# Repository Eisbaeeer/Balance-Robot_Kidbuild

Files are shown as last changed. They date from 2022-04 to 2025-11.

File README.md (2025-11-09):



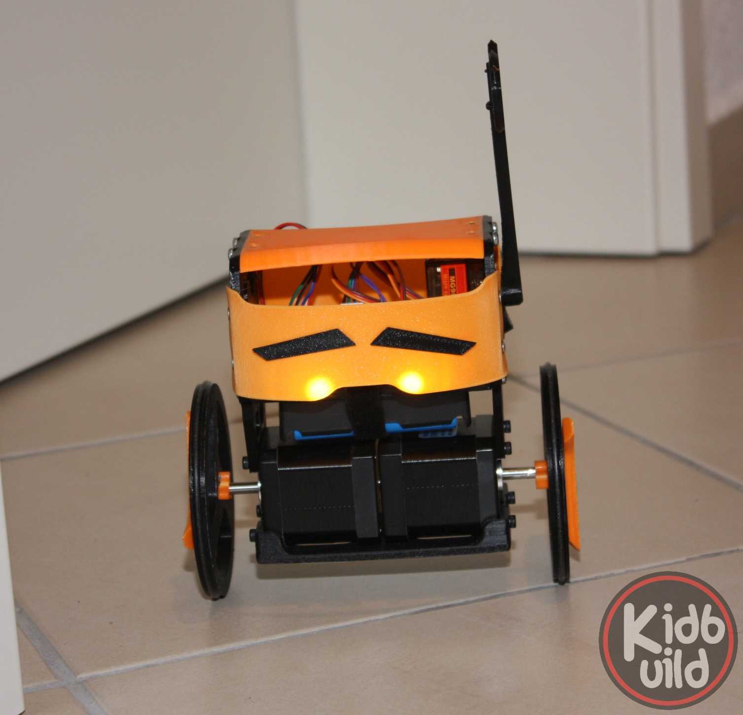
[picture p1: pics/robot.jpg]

# Balance-robot Kidbuild 

## Description
Build your own balanced robot with this project. Based on jjrobots and bluino.com we present an 
open source balanced robot with enhanced features.

## Features
- The source is merged to the platformio enviroment.
- The project is open source. You can build up your own robot for free (only hardware costs).
- The project use standard hardware like stepper, driver, electronics. You can buy it as you like.
- Use the project for education!
- Control the robot via android app

## STL files for 3D printing
You will find all STL files and addons in the STL folder. Typically printed without support.
0.2mm thickness and 20% infill should work well.

## Electronic schematic

| Pin | Function |
|---|---|
| 12 | Stepper A&B Enable | 
| 26 | Stepper A STEP |
| 25 | Stepper A DIR |
| 14 | Stepper B STEP |
| 27 | Stepper B DIR |
| 13 | Servo |
| 21 | MPU-6050 SDA |
| 22 | MPU-6050 SCL |
| 32 | LED Light |
| 33 | BUZZER |

## HMTL commands

| Command Character 	|HTML command after IP/URL  |
|---|---|
| Forward | /?fader1=1.00 |
| Backward | /?fader1=0.00 |
| Turn Right | /?fader2=0.00 |
| Turn Left | /?fader2=1.00 |
| Servo Arm | /?push1=1|2 |
| Beep On|Off 	 | /?push3=1|2 |
| Turn Light On|Off | /?push4=1|0 |
| Mode PRO On|Off | /?toggle1=1|0 |
| P-Stability | /?fader3=0.00-1.00 |
| D-Stability | /?fader4=0.00-1.00 |
| P-Speed | /?fader5=0.00-1.00 |
| I-Speed | /?fader6=0.00-1.00 |

## BOM

| Pieces | Description									|
|---|---|
| 1		 | PCB ESP32 Balancing Robot Shield				|
| 1		 | ESP32 DEVKIT V1 board 						|
| 2		 | Stepper Motor Driver A4988 					|
| 1		 | 3 axis Acc. and Gyro sensor MPU6050 			|
| 2		 | Stepper Motor Nema17 						|
| 1		 | Servo Motor MG90S/SG90						|
| 1		 | LED 3mm red									|
| 2		 | LED 3mm/5mm White Super Bright 				|
| 1		 | Active Buzzer 								|
| 2 	 | V-Regulator 5V AMS1117 SOT-223 (Kit is presoldered)	| 
| 1		 | Resistor 470 Ohm 								|
| 1		 | Capacitor 0.1uF 								|
| 1		 | Capacitor 100uF/16V rad.						| 	
| 2		 | Capacitor 220uF/16V rad.						|
| 1		 | Rocker Switch Dia. 20mm						| 
| 2		 | Rechargeable Battery Pack 2S Li-ion (2x 18650) 		| 
| 1		 | Micro USB Cable (optional for programming)	|
| 1		 | Terminal Screw 2 pin 5mm 					|
| 2		 | Female Header 15 pin 						|
| 5		 | Female Header 8 pin 							|
| 2		 | Female Header 4 pin 							|
| 1		 | Male Header 2 pin 							|
| 1		 | Male Header 3 pin 							|
| 2		 | Male Header 4 pin 							|
| 1		 | Jumper cap 									|
| 2		 | O-ring 3mm ID 82mm							| 
| 8		 | M3x8 screw									| 
| 9		 | M3x10 screw									|
| 9 | M3 nut |
| 12	 | self tapping screws 3mmx3mm					|

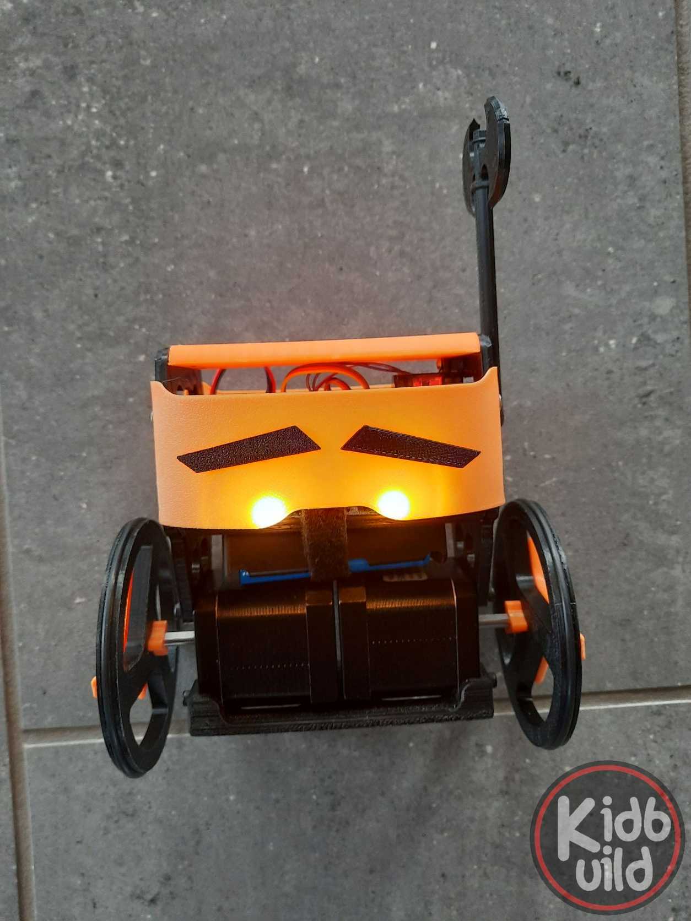
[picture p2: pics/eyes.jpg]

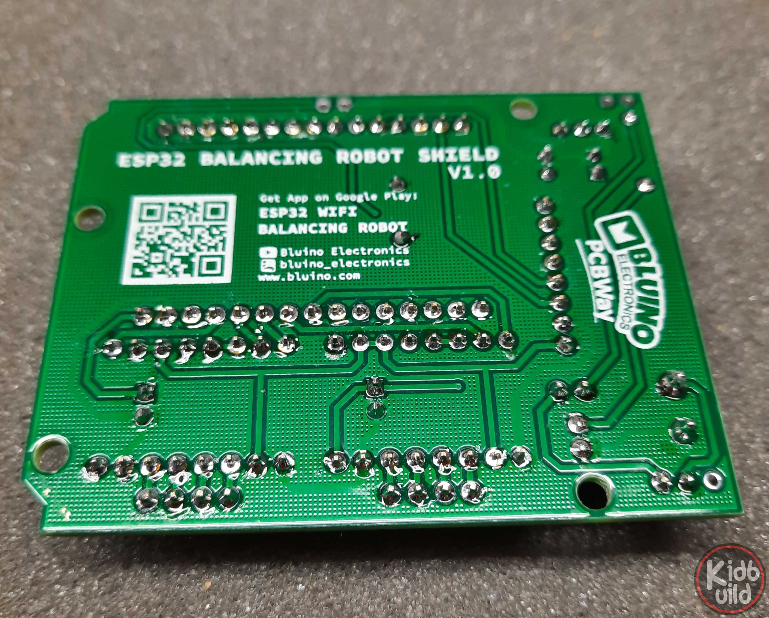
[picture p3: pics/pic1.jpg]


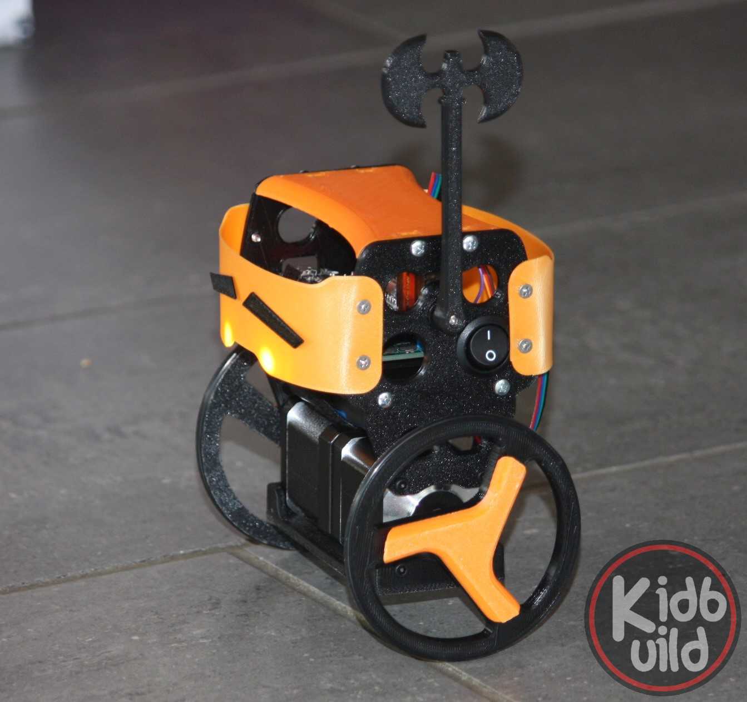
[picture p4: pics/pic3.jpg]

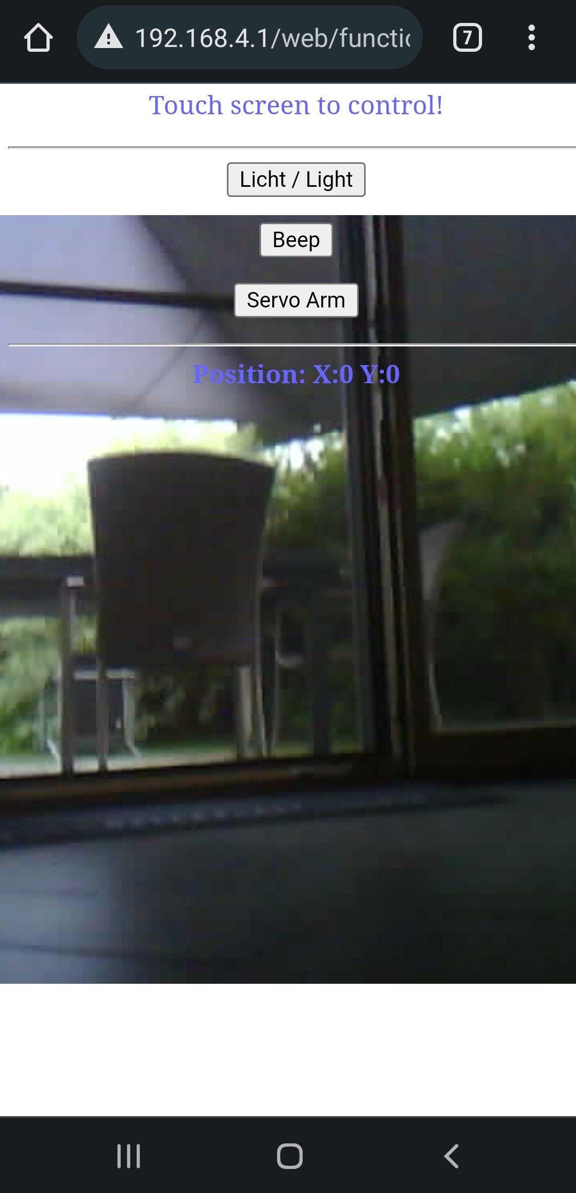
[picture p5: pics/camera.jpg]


## Wii Remote control
- Connect the Wii-Remote by pressing button 1 + 2 in same time
- Wii is connected, if LED one on Wii lit
- Hold the controller horizontal
- Button 1 = piezo
- Button 2 = eyes
- Button A = servo
- Controll via gyro by pressing the B button

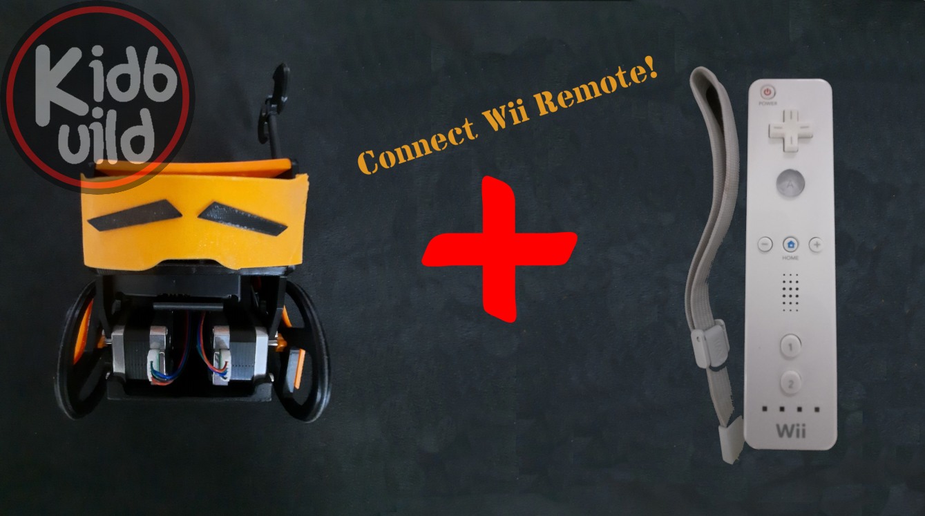
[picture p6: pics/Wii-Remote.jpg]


## How to flash

The easiest way to flash your Robot is to use the web flash tool.
Supported browser: Microsoft Edge or Google Chrome.
Follow this link for easy flashing: https://eisbaeeer.github.io/Balance-Robot_Kidbuild/flash/index.html

### Manual flashing
1. Donwload ESP flasher tool. E.g.: https://github.com/Jason2866/ESP_Flasher/releases
2. Download firmware.bin from release page: https://github.com/Eisbaeeer/Balance-Robot_Kidbuild/releases

## How to update via webUpdate
1. Connect to robot via Wifi
2. Open http://192.168.4.1/update
3. Upload firmware.bin from release page: https://github.com/Eisbaeeer/Balance-Robot_Kidbuild/releases 

## How to compile
1. Install VS-Code
2. Install addon platformio
3. clone repository
4. open repository in VS-Code
4. Compile

## Weblinks to get running
- http://www.kidbuild.de or https://shop.kidbuild.de
E-Mail info@kidbuild.de

## Changelog 

### Version 1.5
    Date: 20220819
    - Added passive buzzer support
    - Robot waiting 45 seconds for Wifi connection. After that the robot will disable Wifi and switch to Wii-remote bluetooth

### Version 1.4
    Date: 20220727
    - Added Wii-Remote as remote controller

### Verison 1.3
    Date: 20220703
    - Added OTA firmware web update
    - Optimized web control

### Version 1.2
	Date: 20220627
	- Added joystick via browser
	- Added background live view with esp32-camera
	- Added light, sound, servo control

### Version 1.0
    Date: 20220529
    Contributor: Kidbuild
    - Added Web control for any browser
    1. Connect to wifi of B-Robot
    2. Open browser at 192.168.4.1
    3. Take control via touch screen

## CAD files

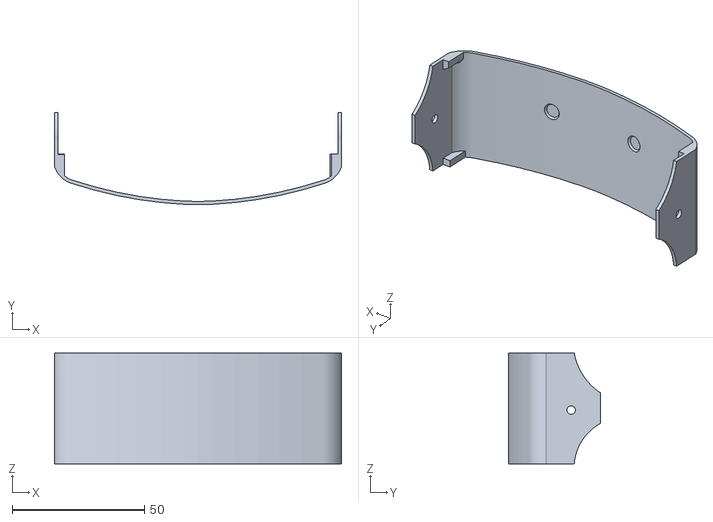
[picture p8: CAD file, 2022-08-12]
STL/2xFixed-Bumper_eyes.stl
108.5 x 34.9 x 41.9

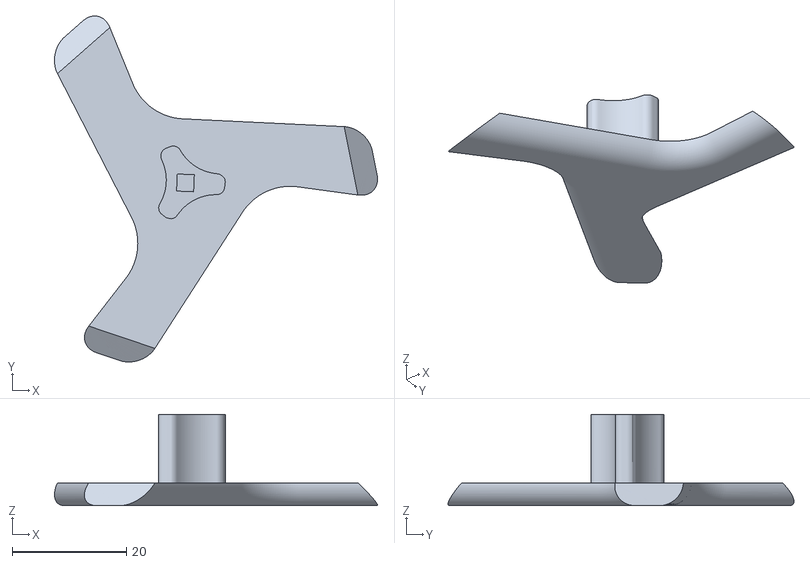
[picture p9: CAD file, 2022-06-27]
STL/Alternate_Hub-Wheel_4edges.stl
56.7 x 60.7 x 16.0

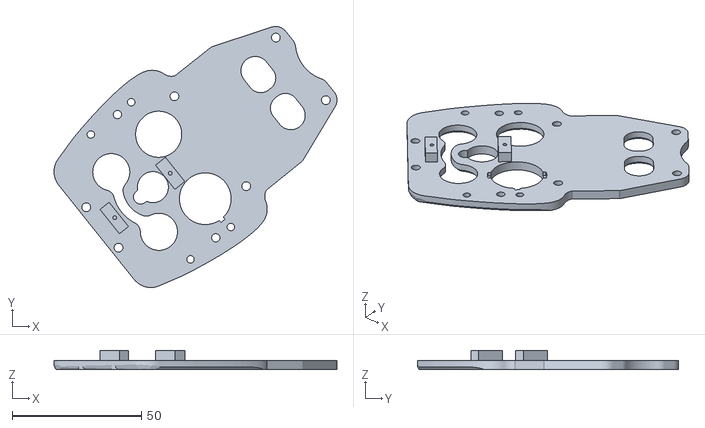
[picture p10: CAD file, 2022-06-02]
STL/1xSide_Panel_left_v3.stl
109.5 x 101.0 x 7.50

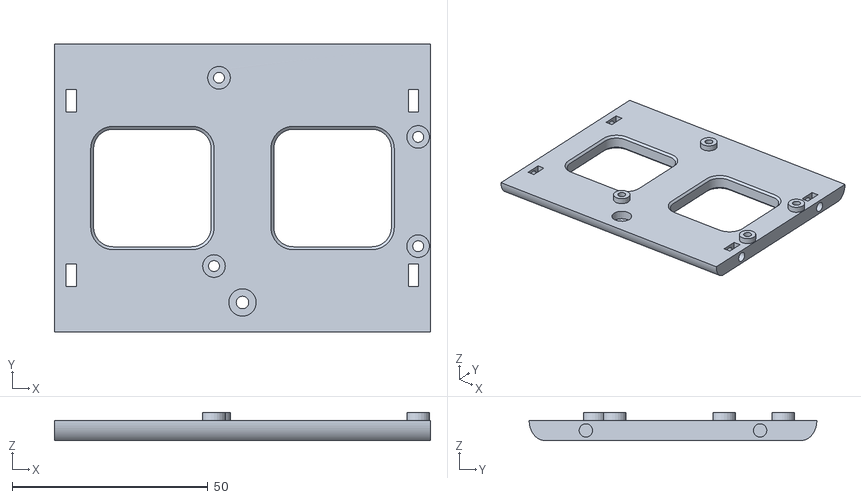
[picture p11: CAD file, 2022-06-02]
STL/1xElectronic_Shelf.stl
96.0 x 73.5 x 7.16

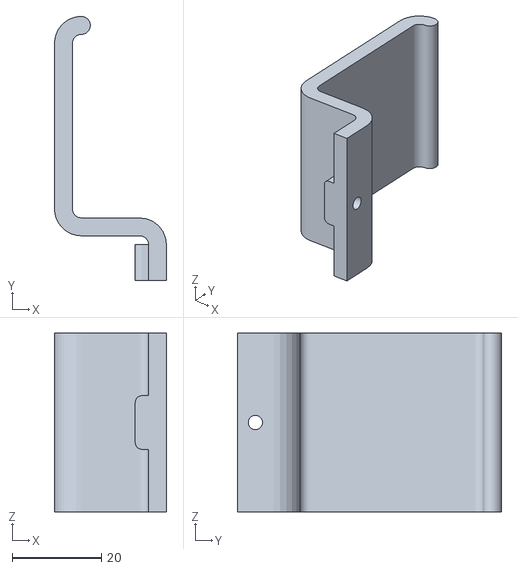
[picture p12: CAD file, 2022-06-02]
STL/1xBattery_holder_clip_2x18650.stl
25.0 x 59.0 x 40.0

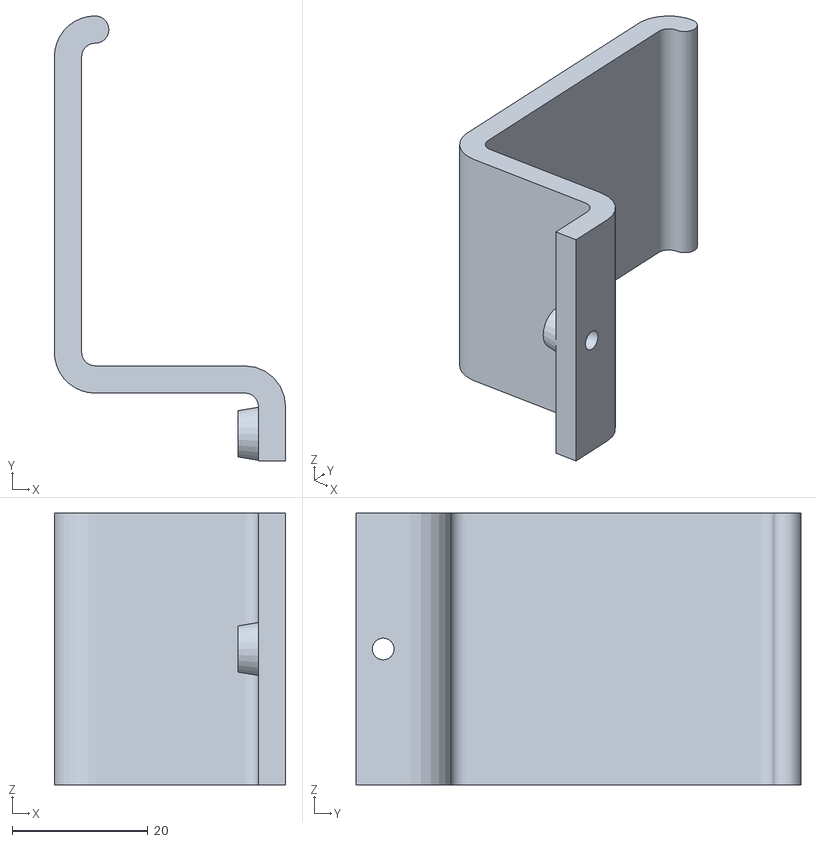
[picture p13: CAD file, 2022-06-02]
STL/1xBattery_holder_clip_6xAA.stl
34.0 x 65.4 x 40.0

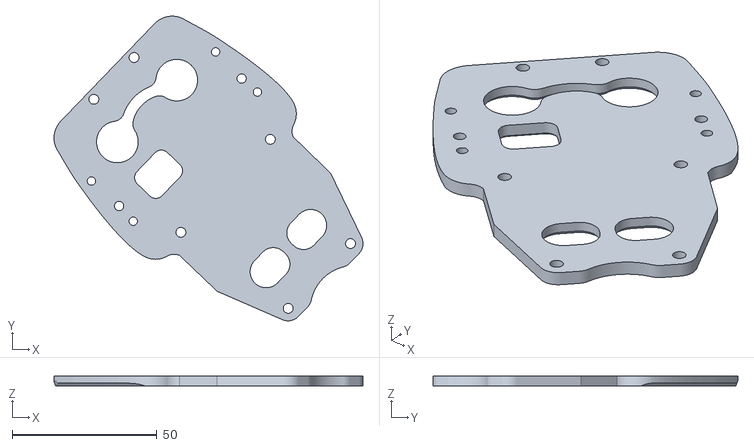
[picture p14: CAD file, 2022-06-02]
STL/1xSide_Panel_right_v3.stl
106.6 x 105.1 x 3.50

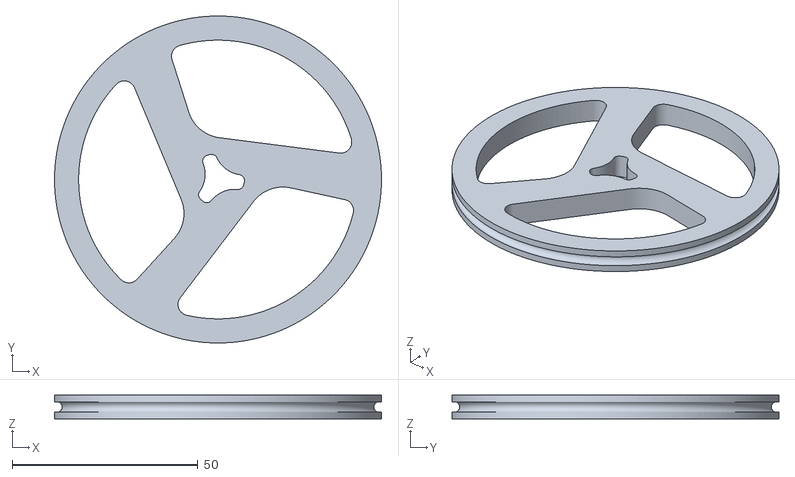
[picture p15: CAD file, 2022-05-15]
STL/2xWheel_FOR_O-RING.stl
88.0 x 88.0 x 6.40

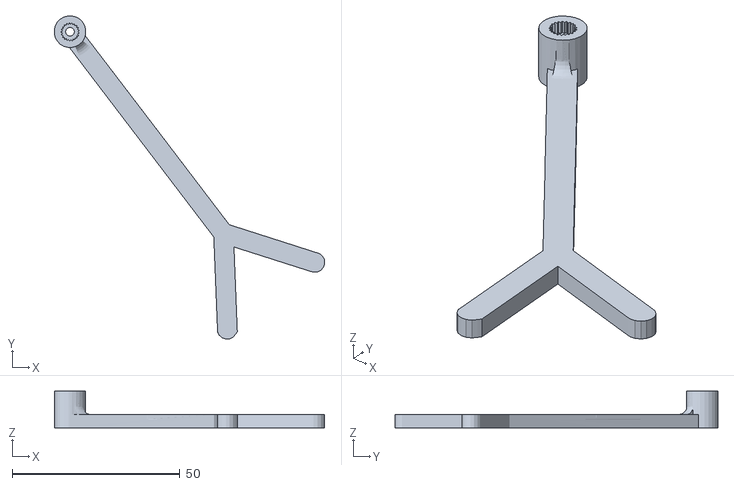
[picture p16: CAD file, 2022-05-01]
STL/1xregular-Arm-5mm.stl
80.6 x 96.3 x 11.0

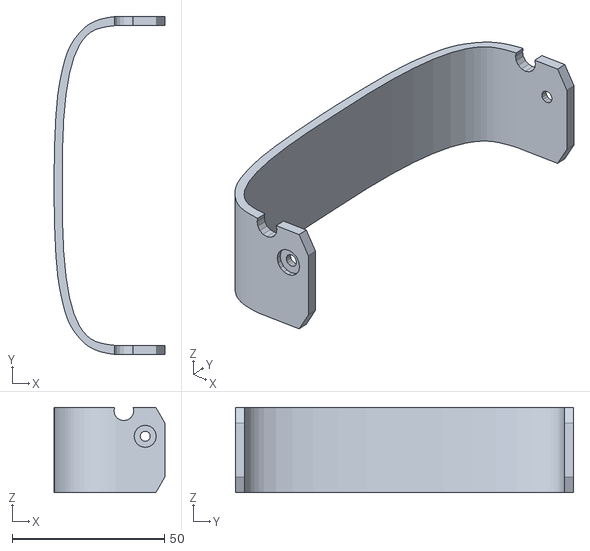
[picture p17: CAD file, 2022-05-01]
STL/ADDON_extra_bumper.stl
36.4 x 111.0 x 28.0

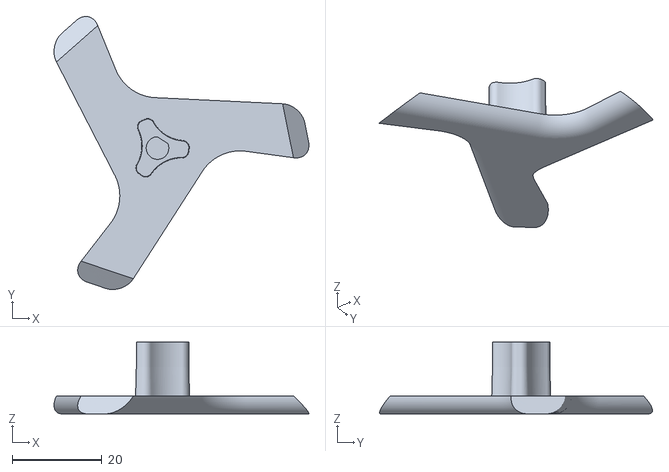
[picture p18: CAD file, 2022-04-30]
STL/2xHub_Wheel_ENLARGED.stl
56.7 x 60.7 x 15.9

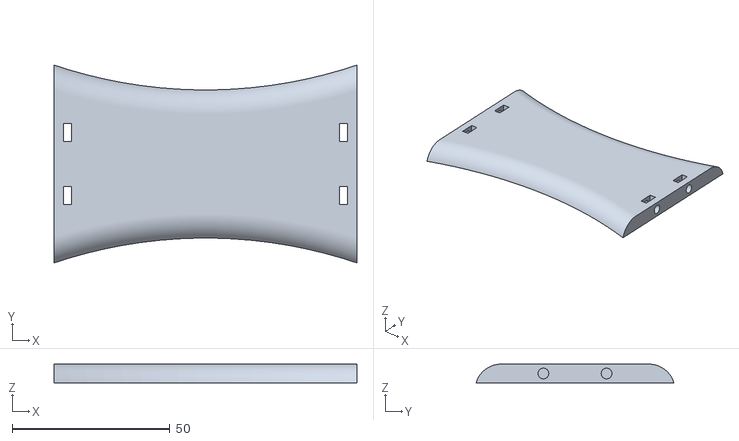
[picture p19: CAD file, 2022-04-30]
STL/1xTop_Shelf.stl
96.0 x 62.7 x 6.00

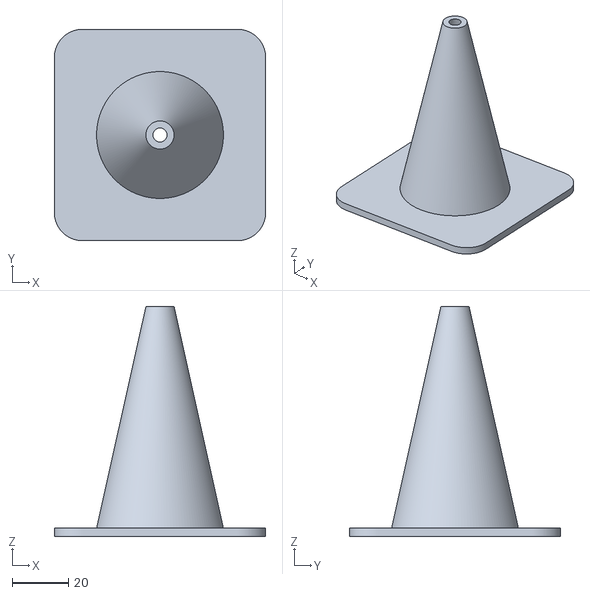
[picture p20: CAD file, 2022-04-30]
STL/ADDON._Traffic_Cone.stl
75.0 x 75.0 x 81.6

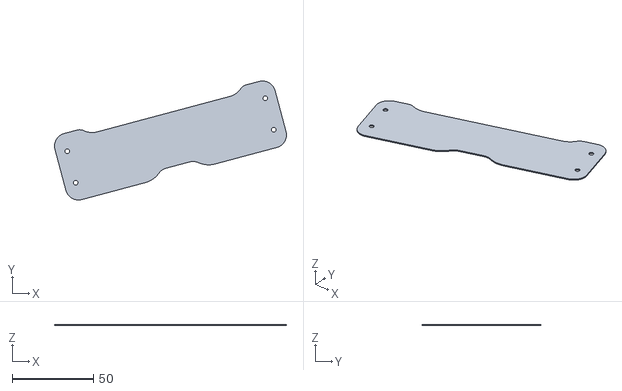
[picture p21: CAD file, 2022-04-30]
STL/2xBUMPER.stl
142.5 x 73.1 x 0.654

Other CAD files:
STL/ADDON_battle_axe_by_jfpion.stl
STL/ADDON_SKULL.stl
STL/ADDON.2xEyebrows.stl
STL/ADDON.1xTop_Shelf_for_CAN.stl
STL/1xMotor_Shelf.stl
STL/1xregular_ARM_6mm.stl
STL/ADDON.Top_Shelf_for_GoPro.stl
STL/ADDON_HOOK_ARM.stl
STL/ADDON_MACE_ARM.stl

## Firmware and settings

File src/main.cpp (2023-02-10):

/*
 *  Created on: 23.02.2021
 *      Author: anonymous
 * 
 *  Changelog:
 * 
 *  ### Version 1.5
 * (20221018)
 * - Added passive buzzer support
 * - Robot waiting 45 seconds for Wifi connection. After that the robot will disable Wifi and switch to Wii-remote bluetooth
 * 
    ### Version 1.4
 *  (20220727)
 *  - Added Wii-Remote as remote controller (pressing key 1 + 2 on same time to connect the Wii Remote)
 * 
 *  ### Verison 1.3
 *  (20220703)
 *  - Added OTA firmware web update
 *  - Optimized web control
 *
 *  ### Version 1.2
 *	(20220627)
 *	- Added joystick via browser
 *	- Added background live view with esp32-came
 *	- Added light, sound, servo control
 *
 *    ### Version 1.0
 *      (20220322)
 *      - Ported to platformio
 *      - Bugfix Android app right/left direction
 * 
 *  ToDo:
 *    - Web-GUI
 *    - OTA
 * 
 * ******** Pin out **********
 * Pin 12   Stepper A&B Enable
 * Pin 26   Stepper A STEP
 * Pin 25   Stepper A DIR
 * Pin 14   Stepper B STEP
 * Pin 27   Stepper B DIR
 * 
 * Pin 13   Servo
 * 
 * Pin 21   MPU-6050 SDA
 * Pin 22   MPU-6050 SCL
 * 
 * Pin 32   LED Light
 * 
 * Pin 33   BUZZER
 * 
 * ******** Command Character *******
 * Forward              /?fader1=1.00
 * Backward             /?fader1=0.00
 * Turn Right           /?fader2=0.00
 * Turn Left            /?fader2=1.00
 * Servo Arm            /?push1=1|2
 * Beep On|Off          /?push3=1|2
 * Turn Light On|Off    /?push4=1|0
 * Mode PRO On|Off      /?toggle1=1|0
 * P-Stability          /?fader3=0.00-1.00
 * D-Stability          /?fader4=0.00-1.00
 * P-Speed              /?fader5=0.00-1.00
 * I-Speed              /?fader6=0.00-1.00
 * 
 * Controll via Wii-Remote controller
 * - Connect to robot = press 1+2 same time
 * - Button 1         = piezo
 * - Button 2         = light
 * - Home             = toggle mode pro (pro mode lights blinking)
 * - Control via gyro = press B button + gyro move to go forward/backward right/left.
 *                      hold controller crosswise
 * 
 */
 
#include <Wire.h>
#include <WiFi.h>
#include <Arduino.h>
#include <AsyncTCP.h>
#include <ESPAsyncWebServer.h>
#include <AsyncElegantOTA.h>
#include "Control.h"
#include "MPU6050.h"
#include "Motors.h"
#include "defines.h"
#include "globals.h"
#include <stdio.h>
#include "esp_types.h"
#include "soc/timer_group_struct.h"
#include "driver/periph_ctrl.h"
#include "driver/timer.h"
#include "driver/ledc.h"
#include "esp32-hal-ledc.h"
#include "ESP32Wiimote.h"


const char* PARAM_FADER1 = "fader1";
const char* PARAM_FADER2 = "fader2";
const char* PARAM_PUSH1 = "push1";
const char* PARAM_PUSH2 = "push2";
const char* PARAM_PUSH3 = "push3";
const char* PARAM_PUSH4 = "push4";
const char* PARAM_TOGGLE1 = "toggle1";
const char* PARAM_FADER3 = "fader3";
const char* PARAM_FADER4 = "fader4";
const char* PARAM_FADER5 = "fader5";
const char* PARAM_FADER6 = "fader6";
//const char joystick_html[] PROGMEM="<html>\n\t <head>\n\t\t <meta charset=\"utf-8\">\n\t\t <meta name=\"viewport\" content=\"width=device-width, user-scalable=no, minimum-scale=1.0, maximum-scale=1.0\">\t\t\n\t\t <style>\n\t\t body {\n\t\t\toverflow\t: hidden;\n\t\t\tpadding\t\t: 0;\n\t\t\tmargin\t\t: 0;\n\t\t\tbackground-image\t: url('http://192.168.4.111:81/stream');\n\t\t\tbackground-repeat\t\t: no-repeat;\n\t\t\t}\n\t\t#info\n\t\t\t{\n\t\t\tcolor\t\t: #66F;\n\t\t\ttext-decoration\t: none;\n\t\t\tposition\t: absolute;\n\t\t\ttop\t\t: 0px;\n\t\t\twidth\t\t: 100%;\n\t\t\tpadding\t\t: 5px;\n\t\t\ttext-align\t: center;\n\t\t}\n\t\t#container {\n\t\t\twidth\t\t: 100%;\n\t\t\theight\t\t: 100%;\n\t\t\toverflow\t: hidden;\n\t\t\tpadding\t\t: 0;\n\t\t\tmargin\t\t: 0;\n\t\t\t-webkit-user-select\t: none;\n\t\t\t-moz-user-select\t: none;\n\t\t}\n\t\t</style>\n\n\t</head>\n\t<body>\n\n\t<div id=\"container\"></div>\n\n\t\n\n\t<div id=\"info\">Touch screen to control!\n\t\t\t<br>\n\t\t\t<p><b><hr><button onclick=\"window.location.href = '/web/function1.html'\">Licht / Light</button>\n\t\t\t<p><b><button onclick=\"window.location.href = '/web/function2.html'\">Beep</button>\n\t\t\t<p><b><button onclick=\"window.location.href = '/web/function3.html'\">Servo Arm</button>\n\t\t\t<hr>\n\t\t\t<span id=\"result\"></span>\n\t\t</div>\n\t\t<script src=\"./virtualjoystick.js\"></script>\n\t\t<script>\n\t\t\tconsole.log(\"touchscreen is\", VirtualJoystick.touchScreenAvailable() ? \"available\" : \"not available\");\n\t\n\t\t\tvar joystick\t= new VirtualJoystick({\n\t\t\t\tcontainer\t: document.getElementById('container'),\n\t\t\t\tmouseSupport\t: true,\n\t\t\t\tlimitStickTravel\t: true,\n\t\t\t});\n\t\t\tjoystick.addEventListener('touchStart', function(){\n\t\t\t\tconsole.log('down')\n\t\t\t})\n\t\t\tjoystick.addEventListener('touchEnd', function(){\n\t\t\t\tconsole.log('up')\n\t\t\t})\n\t\t\tvar prevX = 0;\n\t\t\tvar prevY = 0;\n\t\t\tvar newX = 0;\n\t\t\tvar newY = 0;\n\t\t\tsetInterval(function(){\n\t\t\t\tvar outputEl\t= document.getElementById('result');\n\t\t\t\tnewX = Math.round(joystick.deltaX());\n\t\t\t\tnewY = Math.round(joystick.deltaY()) * -1;\n\t\t\t\toutputEl.innerHTML\t= '<b>Position:</b> '\n\t\t\t\t\t+ ' X:'+newX\n\t\t\t\t\t+ ' Y:'+newY;\n\t\t\t\tif ( newX != prevX || newY != prevY || newX!=0 || newY!=0){\n\t\t\t\t\tvar xhr = new XMLHttpRequest();\n\t\t\t\t\txhr.open('PUT', \"./jsData.html?x=\"+newX+\"&y=\"+newY)\n\t\t\t\t\txhr.send();\n\t\t\t\t\tsetTimeout(function(){xhr.abort();},100);\n\t\t\t\t}\n\t\t\t\tprevX = newX;\n\t\t\t\tprevY = newY;\n\t\t\t}, 150);\n\t\t</script>\n\t</body>\n</html>";
const char joystick_html[] PROGMEM="<html>\n\t <head>\n\t\t <meta charset=\"utf-8\">\n\t\t <meta name=\"viewport\" content=\"width=device-width, user-scalable=no, minimum-scale=1.0, maximum-scale=1.0\">\t\t\n\t\t <style>\n\t\t body {\n\t\t\toverflow\t: hidden;\n\t\t\tpadding\t\t: 0;\n\t\t\tmargin\t\t: 0;\n\t\t\tbackground-image\t: url('http://192.168.4.111:81/stream');\n\t\t\tbackground-repeat\t\t: no-repeat;\n\t\t\tbackground-position: center center;\n\t\t\t}\n\t\t#info\n\t\t\t{\n\t\t\tcolor\t\t: #66F;\n\t\t\ttext-decoration\t: none;\n\t\t\tposition\t: absolute;\n\t\t\ttop\t\t: 0px;\n\t\t\twidth\t\t: 100%;\n\t\t\tpadding\t\t: 5px;\n\t\t\ttext-align\t: center;\n\t\t}\n\t\t#container {\n\t\t\twidth\t\t: 100%;\n\t\t\theight\t\t: 100%;\n\t\t\toverflow\t: hidden;\n\t\t\tpadding\t\t: 0;\n\t\t\tmargin\t\t: 0;\n\t\t\t-webkit-user-select\t: none;\n\t\t\t-moz-user-select\t: none;\n\t\t}\n\t\t</style>\n\n\t</head>\n\t<body>\n\n\t<div id=\"container\"></div>\n\n\t\n\n\t<div id=\"info\">Touch screen to control!\n\t\t\t<br>\n\t\t\t<p><b><hr><button onclick=\"window.location.href = '/web/function1.html'\">Licht / Light</button>\n\t\t\t<p><b><button onclick=\"window.location.href = '/web/function2.html'\">Beep</button>\n\t\t\t<p><b><button onclick=\"window.location.href = '/web/function3.html'\">Servo Arm</button>\n\t\t\t<hr>\n\t\t\t<span id=\"result\"></span>\n\t\t</div>\n\t\t<script src=\"./virtualjoystick.js\"></script>\n\t\t<script>\n\t\t\tconsole.log(\"touchscreen is\", VirtualJoystick.touchScreenAvailable() ? \"available\" : \"not available\");\n\t\n\t\t\tvar joystick\t= new VirtualJoystick({\n\t\t\t\tcontainer\t: document.getElementById('container'),\n\t\t\t\tmouseSupport\t: true,\n\t\t\t\tlimitStickTravel\t: true,\n\t\t\t});\n\t\t\tjoystick.addEventListener('touchStart', function(){\n\t\t\t\tconsole.log('down')\n\t\t\t})\n\t\t\tjoystick.addEventListener('touchEnd', function(){\n\t\t\t\tconsole.log('up')\n\t\t\t})\n\t\t\tvar prevX = 0;\n\t\t\tvar prevY = 0;\n\t\t\tvar newX = 0;\n\t\t\tvar newY = 0;\n\t\t\tsetInterval(function(){\n\t\t\t\tvar outputEl\t= document.getElementById('result');\n\t\t\t\tnewX = Math.round(joystick.deltaX());\n\t\t\t\tnewY = Math.round(joystick.deltaY()) * -1;\n\t\t\t\toutputEl.innerHTML\t= '<b>Position:</b> '\n\t\t\t\t\t+ ' X:'+newX\n\t\t\t\t\t+ ' Y:'+newY;\n\t\t\t\tif ( newX != prevX || newY != prevY || newX!=0 || newY!=0){\n\t\t\t\t\tvar xhr = new XMLHttpRequest();\n\t\t\t\t\txhr.open('PUT', \"./jsData.html?x=\"+newX+\"&y=\"+newY)\n\t\t\t\t\txhr.send();\n\t\t\t\t\tsetTimeout(function(){xhr.abort();},100);\n\t\t\t\t}\n\t\t\t\tprevX = newX;\n\t\t\t\tprevY = newY;\n\t\t\t}, 150);\n\t\t</script>\n\t</body>\n</html>";
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
void loop() {

  //task A
    if (taskA.previous == 0 || (millis() - taskA.previous > taskA.rate)) {
        taskA.previous = millis(); 
        // 500 ms
        
        if (fromWeb) {
          fromWeb == 0;
          if (OSCpush[0]) {
            OSCpush[0]=0;
          }
        }
        action = true;  // debounce actions

        // blinking eyes during PRO MODE
        if (OSCtoggle[0] == 1) {
            digitalWrite(PIN_LED, !digitalRead(PIN_LED));
        }

        ledcWriteTone(channel, 0);

        if (wifiTimeout) {
          digitalWrite (PIN_WIFI_LED, !digitalRead(PIN_WIFI_LED));
        }
    }

  //task B
    if (taskB.previous == 0 || (millis() - taskB.previous > taskB.rate)) {
        taskB.previous = millis(); 
        // 1000 ms

        wifiSeconds++;

        if ((wifiSeconds > 45) && (WiFi.softAPgetStationNum() == 0)) {
          wifiTimeout = true;
        }
    }


  if (OSCnewMessage) {
    OSCnewMessage = 0;
    processOSCMsg();
  }

  
  if (wifiTimeout) {
    /* Wii-Remote */
      wiimote.task();
      num_run++;

      if (wiimote.available() > 0) {
        ButtonState  button  = wiimote.getButtonState();
        AccelState   accel   = wiimote.getAccelState();
        NunchukState nunchuk = wiimote.getNunchukState();

        num_updates++;

        /* process buttons from Wii */
        
        // Servo
        if (button & BUTTON_A) {
          if (action) { 
            taskA.previous = millis();
            action = false;
            fromWeb = 1;
            OSCpage = 1;
            OSCpush[0]=1;
          }
        }
        if (button & BUTTON_ONE) {
            // toggle need
          if (action) {  
            taskA.previous = millis();
            action = false;
            playsound();
          }
        }
        if (button & BUTTON_TWO) {
            // toggle need
          if (action) { 
            taskA.previous = millis(); 
            action = false;
            digitalWrite(PIN_LED, !digitalRead(PIN_LED));
          }
        }
        // Switch ProMode
        if (button & BUTTON_HOME) {
            // toggle need         
          if (action) { 
            taskA.previous = millis(); 
            action = false;
            if (OSCtoggle[0] == 1) {
                OSCtoggle[0] = 0;
            } else {
                OSCtoggle[0] = 1;
            }
          }
        }

        // Calculate Forward/Backward Left/Right
  
      if (button & BUTTON_B) {

        switch (accel.xAxis) {
          case 98: OSCfader[0] = 0.175; break;
          case 99: OSCfader[0] = 0.175; break;
          case 100: OSCfader[0] = 0.2; break;
          case 101: OSCfader[0] = 0.2; break;
          case 102: OSCfader[0] = 0.225; break;
          case 103: OSCfader[0] = 0.225; break;
          case 104: OSCfader[0] = 0.25; break;
          case 105: OSCfader[0] = 0.25; break;
          case 106: OSCfader[0] = 0.275; break;
          case 107: OSCfader[0] = 0.275; break;
          case 108: OSCfader[0] = 0.3; break;
          case 109: OSCfader[0] = 0.3; break;
          case 110: OSCfader[0] = 0.325; break;
          case 111: OSCfader[0] = 0.325; break;
          case 112: OSCfader[0] = 0.35; break;
          case 113: OSCfader[0] = 0.35; break;
          case 114: OSCfader[0] = 0.375; break;
          case 115: OSCfader[0] = 0.375; break;
          case 116: OSCfader[0] = 0.4; break;
          case 117: OSCfader[0] = 0.4; break;
          case 118: OSCfader[0] = 0.425; break;
          case 119: OSCfader[0] = 0.425; break;
          case 120: OSCfader[0] = 0.45; break;
          case 121: OSCfader[0] = 0.45; break;
          case 122: OSCfader[0] = 0.475; break;
          case 123: OSCfader[0] = 0.475; break;       
          case 124: OSCfader[0] = 0.5; break;
          case 125: OSCfader[0] = 0.525; break;
          case 126: OSCfader[0] = 0.525; break;
          case 127: OSCfader[0] = 0.55; break;
          case 128: OSCfader[0] = 0.55; break;
          case 129: OSCfader[0] = 0.6; break;
          case 130: OSCfader[0] = 0.6; break;
          case 131: OSCfader[0] = 0.625; break;
          case 132: OSCfader[0] = 0.625; break;
          case 133: OSCfader[0] = 0.65; break;
          case 134: OSCfader[0] = 0.65; break;
          case 135: OSCfader[0] = 0.675; break;
          case 136: OSCfader[0] = 0.675; break;
          case 137: OSCfader[0] = 0.7; break;
          case 138: OSCfader[0] = 0.7; break;
          case 139: OSCfader[0] = 0.725; break;
          case 140: OSCfader[0] = 0.725; break;
          case 141: OSCfader[0] = 0.75; break;
          case 142: OSCfader[0] = 0.75; break;
          case 143: OSCfader[0] = 0.775; break;
          case 144: OSCfader[0] = 0.775; break;
          case 145: OSCfader[0] = 0.8; break;
          case 146: OSCfader[0] = 0.8; break;
          case 147: OSCfader[0] = 0.825; break;
          case 148: OSCfader[0] = 0.825; break;
        }

      switch (accel.xAxis) {
          case 98: OSCfader[0] = 0.175; break;
          case 99: OSCfader[0] = 0.175; break;
          case 100: OSCfader[0] = 0.2; break;
          case 101: OSCfader[0] = 0.2; break;
          case 102: OSCfader[0] = 0.225; break;
          case 103: OSCfader[0] = 0.225; break;
          case 104: OSCfader[0] = 0.25; break;
          case 105: OSCfader[0] = 0.25; break;
          case 106: OSCfader[0] = 0.275; break;
          case 107: OSCfader[0] = 0.275; break;
          case 108: OSCfader[0] = 0.3; break;
          case 109: OSCfader[0] = 0.3; break;
          case 110: OSCfader[0] = 0.325; break;
          case 111: OSCfader[0] = 0.325; break;
          case 112: OSCfader[0] = 0.35; break;
          case 113: OSCfader[0] = 0.35; break;
          case 114: OSCfader[0] = 0.375; break;
          case 115: OSCfader[0] = 0.375; break;
          case 116: OSCfader[0] = 0.4; break;
          case 117: OSCfader[0] = 0.4; break;
          case 118: OSCfader[0] = 0.425; break;
          case 119: OSCfader[0] = 0.425; break;
          case 120: OSCfader[0] = 0.45; break;
          case 121: OSCfader[0] = 0.45; break;
          case 122: OSCfader[0] = 0.475; break;
          case 123: OSCfader[0] = 0.475; break;       
          case 124: OSCfader[0] = 0.5; break;
          case 125: OSCfader[0] = 0.525; break;
          case 126: OSCfader[0] = 0.525; break;
          case 127: OSCfader[0] = 0.55; break;
          case 128: OSCfader[0] = 0.55; break;
          case 129: OSCfader[0] = 0.6; break;
          case 130: OSCfader[0] = 0.6; break;
          case 131: OSCfader[0] = 0.625; break;
          case 132: OSCfader[0] = 0.625; break;
          case 133: OSCfader[0] = 0.65; break;
          case 134: OSCfader[0] = 0.65; break;
          case 135: OSCfader[0] = 0.675; break;
          case 136: OSCfader[0] = 0.675; break;
          case 137: OSCfader[0] = 0.7; break;
          case 138: OSCfader[0] = 0.7; break;
          case 139: OSCfader[0] = 0.725; break;
          case 140: OSCfader[0] = 0.725; break;
          case 141: OSCfader[0] = 0.75; break;
          case 142: OSCfader[0] = 0.75; break;
          case 143: OSCfader[0] = 0.775; break;
          case 144: OSCfader[0] = 0.775; break;
          case 145: OSCfader[0] = 0.8; break;
          case 146: OSCfader[0] = 0.8; break;
          case 147: OSCfader[0] = 0.825; break;
          case 148: OSCfader[0] = 0.825; break;
        }
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

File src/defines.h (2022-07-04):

/*
 * defines.h
 *
 *  Created on: 25.09.2017
 *      Author: anonymous
 */

#ifndef DEFINES_H_
#define DEFINES_H_

#define PIN_ENABLE_MOTORS 12        
#define PIN_MOTOR1_DIR 27    
#define PIN_MOTOR1_STEP 14    
#define PIN_MOTOR2_DIR 25    
#define PIN_MOTOR2_STEP 26   
#define PIN_SERVO 13    
#define PIN_LED 32         
#define PIN_WIFI_LED 2        
#define PIN_BUZZER 33         

// NORMAL MODE PARAMETERS (MAXIMUN SETTINGS)
#define MAX_THROTTLE 550
#define MAX_STEERING 140
#define MAX_TARGET_ANGLE 14

// PRO MODE = MORE AGGRESSIVE (MAXIMUN SETTINGS)
#define MAX_THROTTLE_PRO 780   // Max recommended value: 860
#define MAX_STEERING_PRO 260   // Max recommended value: 280
#define MAX_TARGET_ANGLE_PRO 26   // Max recommended value: 32

// Default control terms for EVO 2
#define KP 0.32
#define KD 0.050
#define KP_THROTTLE 0.080
#define KI_THROTTLE 0.1
#define KP_POSITION 0.06
#define KD_POSITION 0.45
//#define KI_POSITION 0.02

// Control gains for raiseup (the raiseup movement requiere special control parameters)
#define KP_RAISEUP 0.1
#define KD_RAISEUP 0.16
#define KP_THROTTLE_RAISEUP 0.0   // No speed control on raiseup
#define KI_THROTTLE_RAISEUP 0.0

#define MAX_CONTROL_OUTPUT 500
#define ITERM_MAX_ERROR 30   // Iterm windup constants for PI control
#define ITERM_MAX 10000

#define ANGLE_OFFSET 0.0  // Offset angle for balance (to compensate robot own weight distribution)

// Servo definitions        max range of servo is 8400
#define SERVO_AUX_NEUTRO 4444  // Servo neutral position
#define SERVO_MIN_PULSEWIDTH SERVO_AUX_NEUTRO - 3300        //back  
#define SERVO_MAX_PULSEWIDTH SERVO_AUX_NEUTRO + 4000        //front

#define SERVO2_NEUTRO 4444
#define SERVO2_RANGE 8400

#define ZERO_SPEED 0xffffff
#define MAX_ACCEL 14      // Maximun motor acceleration (MAX RECOMMENDED VALUE: 20) (default:14)

#define MICROSTEPPING 8   // 8 or 16 for 1/8 or 1/16 driver microstepping (default:16)

// AUX definitions
#define CLR(x,y) (x&=(~(1<<y)))
#define SET(x,y) (x|=(1<<y))
#define RAD2GRAD 57.2957795
#define GRAD2RAD 0.01745329251994329576923690768489

#endif /* DEFINES_H_ */

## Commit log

2022-04-30 Added some files
    Added STL files and BOM in README.md
    [1xElectronics_Shelf.stl, 1xMotor_Shelf.stl, 1xSide_Panel_left_v2.stl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]
2022-05-01 Update
    updated pictures
    [1xregular-Arm-5mm.stl, 1xregular_ARM_5mm.stl, ADDON_extra_bumper.stl]
2022-06-02 Update STL and firmware
    Updated STL see README.md
    [1xBattery_holder_clip_2x18650.stl, 1xBattery_holder_clip_6xAA.stl, 1xElectronic_Shelf.stl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]
2022-06-27 Version 1.2
    Details see README.md
    [Alternate_Hub-Wheel_4edges.stl]
2022-07-04 Version 1.3
    changed servo settings for riseup
2022-08-12 Added 3D prints
    Added bumper
    [2xFixed-Bumper_eyes.stl]
2022-08-21 Version 1.5
    - Added passive buzzer support
    - Robot waiting 45 seconds for Wifi connection. After that the robot will disable Wifi and switch to Wii-remote bluetooth
    [globals.cpp, main.cpp]
2023-02-13 Add webflash tool
    Adding tool to flash ESP32 via Chrome & Edge
2023-03-22 Update BOM
2023-10-16 Update README.md
    Added Male Header 4 pin in BOM
2025-11-09 updated BOM
